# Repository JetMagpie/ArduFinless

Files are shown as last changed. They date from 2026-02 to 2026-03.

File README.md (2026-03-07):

# ArduFinless
An arduino based finless flying wing project, includes sideslip angle detection and drag rudder control law design.

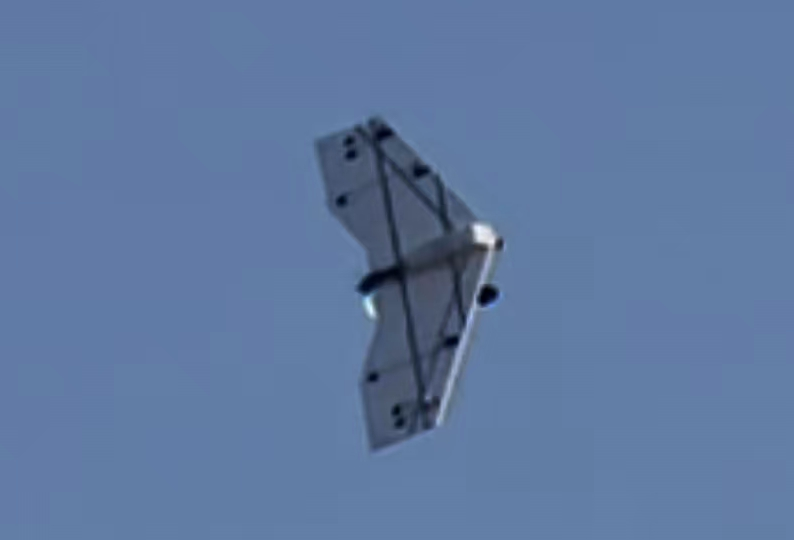
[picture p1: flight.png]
flight


**All engineering source files (.dxf, .step, .stp, .stl, .cpp, .h, .ino) of this project are licensed under the CERN-OHL-S-2.0 license, unless otherwise stated within the specific file.**

# Setup
The default code is written for arduino mega 2560 with a AS5047p as sideslip angle sensor and a mpu6500 as gyro. The sideslip angle sensor needs 4 m2.5x4 screws, a m3*10 screw and two 5x8x2 bearings to assemble. 

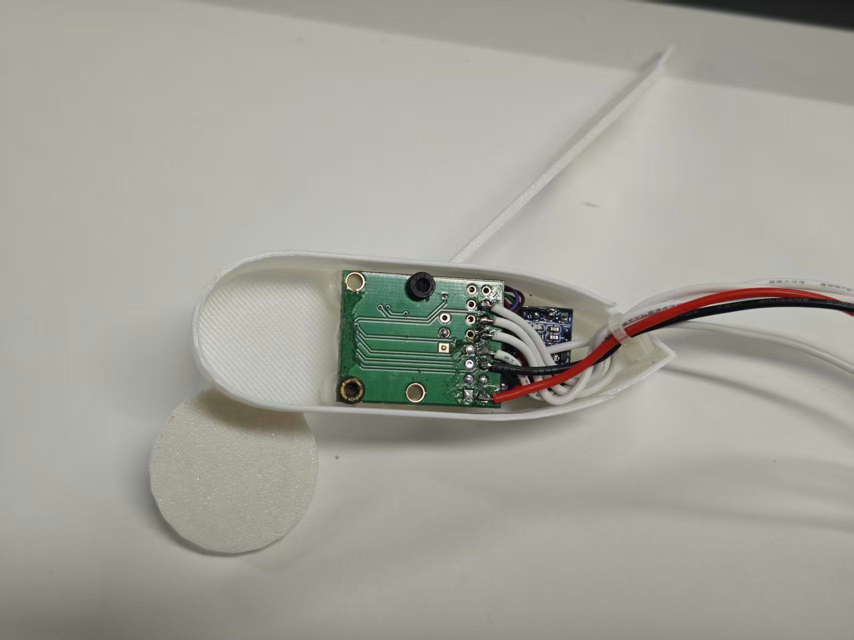
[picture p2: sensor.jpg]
sensor


The default airframe is made of 2mm foam board (vector board, depron, etc.) and 2mm carbon fiber rods. A detailed STP file and a laser engraver friendly dxf file are provided. Recommended electronic devices are KST ds113mg servos, xing2205 motor with 5040 propeller (20a ESC recommended) and 1000mAh3S LiPo battery. 

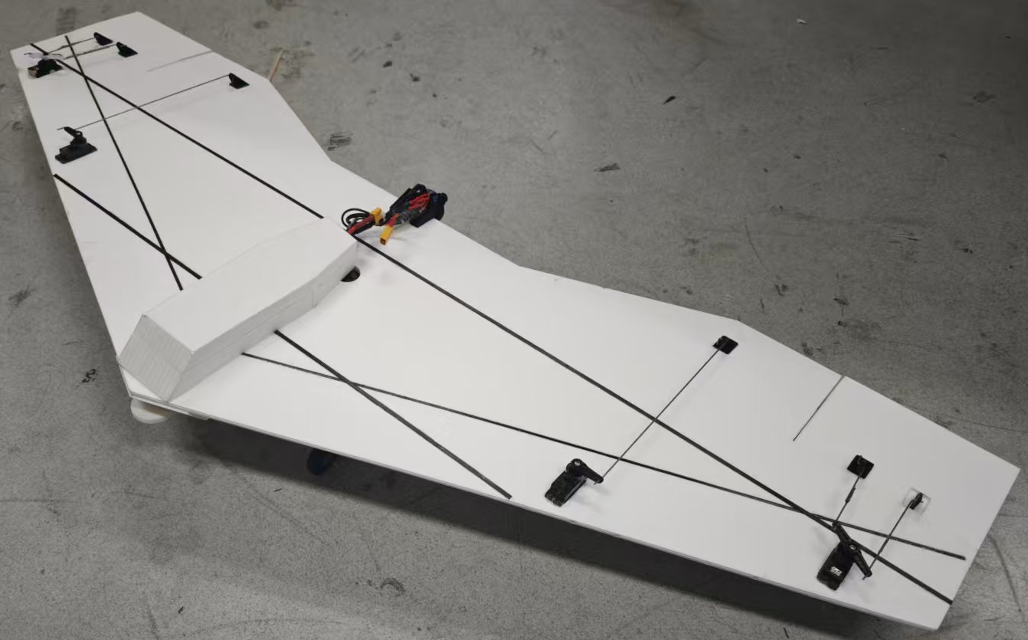
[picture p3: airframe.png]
airframe


The wiring is shown in this figure:

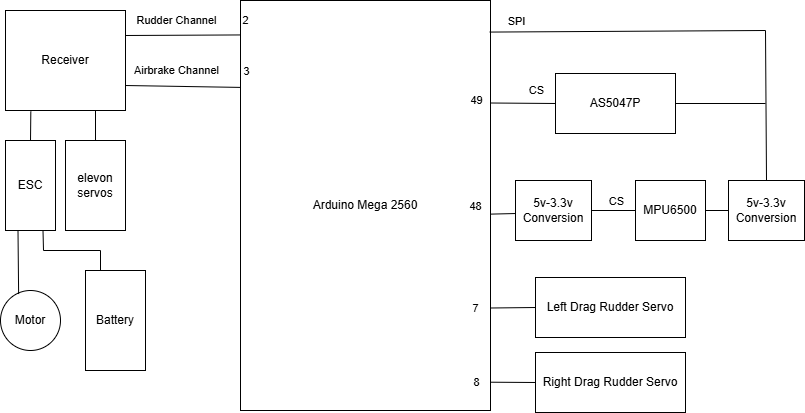
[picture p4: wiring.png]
wiring


# Parameters
Parameters can be changed via serial (baud rate 115200), send `help` to serial to see instructions.

It is recommended to change `right_lim_inf`, `right_lim_sup`, `left_lim_inf`, `left_lim_sup` to fit your servo installation, change `encoder_calibration` and `gyro_calibration` to fit your sensor installation, and change `Cn_beta` (coefficient of sideslip angle) and `Cn_damper` (coefficient of yaw rate) to fit your aircraft design. `Cn_y` can be used as an alternative of `Cn_beta`, it estimates beta with lateral acceleration.

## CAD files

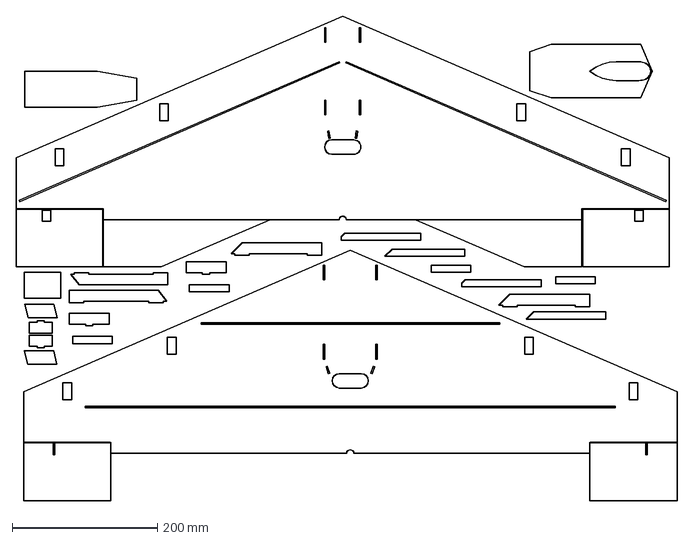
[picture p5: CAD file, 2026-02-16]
miniflywing_2mm.dxf
910.5 x 666.9 mm

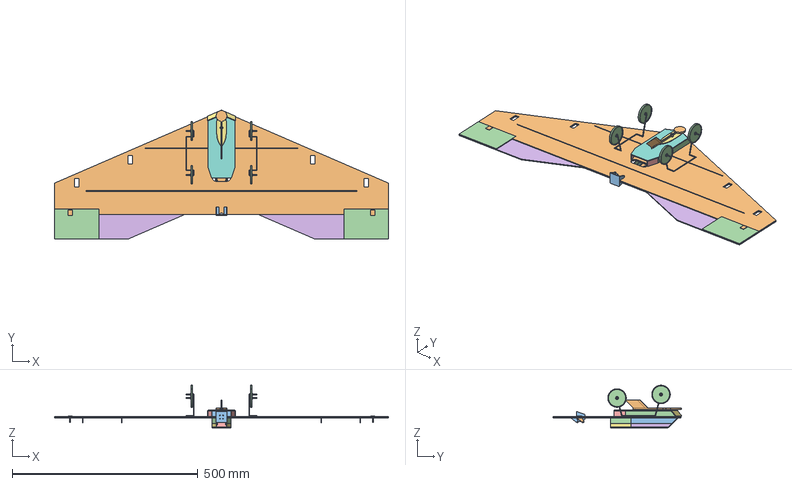
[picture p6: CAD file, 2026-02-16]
miniflywing.stp
900.0 x 346.5 x 115.0 mm

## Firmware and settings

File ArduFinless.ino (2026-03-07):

/*
 * 主程序：阻力舵飞翼控制程序（带串口调参与EEPROM存储）
 * 功能：
 * 1. 读取AS5047P磁编码器角度并处理过零点
 * 2. 读取MPU6500陀螺仪Z轴角速度
 * 3. 读取PWM输入并归一化
 * 4. 所有传感器输入经过低通滤波
 * 5. 根据阻力舵控制律计算右左输出值
 * 6. 输出PWM控制信号
 * 7. 串口调参：report/get/set/help/params
 * 8. 参数自动保存到EEPROM（启动时加载）
 */

#include <Arduino.h>
#include <SPI.h>
#include <EEPROM.h>
#include "PWM_IO.h"
#include "MPU6500.h"
#include "AS5047P.h" 
#include "LowPassFilter.h"

// ==================== 引脚定义 ====================
#define ENCODER_CS_PIN 49  // AS5047P的CS引脚
#define IMU_CS_PIN 48      // MPU6500的CS引脚

// ==================== 全局对象 ====================
PWM_IO pwmIO;
MPU6500 imu(IMU_CS_PIN, false); // 使用MPU6500库
AS5047P encoder(ENCODER_CS_PIN); // 使用AS5047P库

// ==================== 低通滤波器实例 ====================
const float SAMPLE_TIME = 0.01f;       // 采样时间10ms (100Hz)
float beta_cutoff_freq = 50.0f;        // 角度截止频率 (Hz)
float gyro_cutoff_freq = 50.0f;        // 角速度截止频率 (Hz)
float yaw_cutoff_freq = 80.0f;         // Yaw输入截止频率 (Hz)
float brake_cutoff_freq = 80.0f;       // Brake输入截止频率 (Hz)
float accel_cutoff_freq = 50.0f;       // 侧力截止频率 (Hz)

LowPassFilter beta_filter(beta_cutoff_freq, SAMPLE_TIME);
LowPassFilter gyro_filter(gyro_cutoff_freq, SAMPLE_TIME);
LowPassFilter accel_filter(accel_cutoff_freq, SAMPLE_TIME);

// ==================== 可调参数（将存入EEPROM）====================
// 这些全局变量将在加载EEPROM后被赋值
uint16_t right_lim_inf = 1600;   // 右输出最小脉冲宽度（微秒）
uint16_t right_lim_sup = 1800;   // 右输出最大脉冲宽度（微秒）
uint16_t left_lim_inf = 1200;    // 左输出最小脉冲宽度（微秒）
uint16_t left_lim_sup = 1400;    // 左输出最大脉冲宽度（微秒）
float encoder_calibration = 0.0f;// 编码器角度校准量（度）
float gyro_calibration = 0.0f;   // 陀螺仪角速度校准量（度/秒）
float Cn_beta = 5.0f;            // 角度反馈增益
float Cn_damper = 1.0f;          // 阻尼增益
float Cn_y = 1.0f;               // 侧力补偿

// 固定参数
float Yaw_gain = 1.0f;                 // 摇杆增益

// ==================== EEPROM 存储相关 ====================
#define EEPROM_MAGIC 0xDEADBEEF        // 用于校验EEPROM是否有效

// 参数结构体（紧凑排列，无填充）
struct SystemParams {
    uint16_t right_lim_inf;
    uint16_t right_lim_sup;
    uint16_t left_lim_inf;
    uint16_t left_lim_sup;
    float encoder_calibration;
    float gyro_calibration;
    float Cn_beta;
    float Cn_damper;
    float Cn_y;
} __attribute__((packed));

// 配置结构体（包含魔法数）
struct Config {
    uint32_t magic;
    SystemParams params;
} __attribute__((packed));

// 参数名称与范围（用于串口调参）
const char* param_names[] = {
    "right_lim_inf",
    "right_lim_sup", 
    "left_lim_inf",
    "left_lim_sup",
    "encoder_calibration",
    "gyro_calibration",
    "Cn_beta",
    "Cn_damper",
    "Cn_y"
};

struct ParamRange {
    float min;
    float max;
};

const ParamRange param_ranges[] = {
    {800, 2200},   // right_lim_inf
    {800, 2200},   // right_lim_sup
    {800, 2200},   // left_lim_inf
    {800, 2200},   // left_lim_sup
    {-360.0, 360.0},     // encoder_calibration
    {-10.0, 10.0},       // gyro_calibration
    {-50.0, 50.0},       // Cn_beta
    {-50.0, 50.0},       // Cn_damper
    {-50.0, 50.0}        // Cn_y
};
const int NUM_PARAMS = sizeof(param_names) / sizeof(char*);

// 默认参数值（与初始化值一致）
const SystemParams DEFAULT_PARAMS = {
    1600,   // right_lim_inf
    1800,   // right_lim_sup
    1200,    // left_lim_inf
    1400,   // left_lim_sup
    0.0f, // encoder_calibration
    0.0f,    // gyro_calibration
    5.0f,    // Cn_beta
    1.0f,    // Cn_damper
    1.0f     //Cn_y
};

// 串口命令相关
volatile bool report_enabled = false;   // 默认关闭调试打印
char serial_buffer[64];
uint8_t serial_index = 0;

// ==================== 函数声明 ====================
float readEncoderAngle(float calibration);
float readGyroRate(float calibration);
float readAccelY();
void readPWMInputs(float& Yaw, float& Brake);
void calculateOutputs(float Yaw, float Brake, float Beta, float Yaw_Rate, 
                     float Yaw_gain, float Cn_beta, float Cn_damper,
                     float& OUT_right, float& OUT_left);
void setPWMOutputs(float OUT_right, float OUT_left,
                   uint16_t right_lim_inf, uint16_t right_lim_sup,
                   uint16_t left_lim_inf, uint16_t left_lim_sup);
float normalizeAngle(float angle_deg);
void printDebugInfo(float Beta_raw, float Beta_filtered, float Yaw_Rate_raw, float Yaw_Rate_filtered,
                    float Yaw_raw, float Yaw_filtered, float Brake_raw, float Brake_filtered,
                    float OUT_right, float OUT_left);

// 新增串口与EEPROM函数
void loadParamsFromEEPROM();
void saveParamsToEEPROM();
void processSerialInput();
void processSerialCommand();
bool validateParam(int index, float value);
void printAllParams();

// ==================== 主程序 ====================

void setup() {
  // 初始化串口通信
  Serial.begin(115200);
  delay(100);
  
  // 从EEPROM加载参数（会更新全局变量）
  loadParamsFromEEPROM();
 
  // 初始化PWM输入输出
  pwmIO.begin();
  Serial.println("PWM IO initialized");
  
  // 初始化SPI
  SPI.begin();
  SPI.setClockDivider(SPI_CLOCK_DIV128);  // 设置100kHz时钟
  
  // 初始化磁编码器
  if (encoder.init()) {
    Serial.println("AS5047P initialized");
  } else {
    Serial.println("AS5047P initialization failed");
  }
  
  // 初始化陀螺仪
  if (imu.init()) {
    Serial.println("MPU6500 initialized");
  } else {
    Serial.println("MPU6500 initialization failed");
  }
  
  // 启用所有PWM输出通道
  pwmIO.enableOutput(1);
  pwmIO.enableOutput(2);
  pwmIO.enableOutput(3);
  pwmIO.enableOutput(4);
  
  Serial.println("System initialized");
  Serial.println("Serial commands: report on/off, get <param>, set <param> <value>, help, params");
  Serial.println("Data reporting is OFF by default. Use 'report on' to enable.");
  Serial.println("===================================");
  delay(1000);
}

void loop() {
  static uint32_t last_print_time = 0;
  static uint32_t last_update_time = 0;
  
  // 处理串口输入（调参命令）
  processSerialInput();
  
  // 检查PWM输入超时
  pwmIO.checkTimeouts();
  
  // 读取编码器原始角度（Beta）
  float Beta_raw = readEncoderAngle(encoder_calibration);
  
  // 读取陀螺仪原始角速度（Yaw_Rate）
  float Yaw_Rate_raw = readGyroRate(gyro_calibration);

    // 读取陀螺仪原始侧力(Accel_y)
  float Accel_y_raw = readAccelY();
  
  // 读取PWM输入（Yaw和Brake）
  float Yaw = 0.0f, Brake = 0.0f;
  readPWMInputs(Yaw, Brake);
  
  // 应用低通滤波
  float Beta = beta_filter.update(Beta_raw);
  float Yaw_Rate = gyro_filter.update(Yaw_Rate_raw);
  float Accel_y = accel_filter.update(Accel_y_raw);
  
  // 计算输出值
  static float OUT_right = 0.0f;
  static float OUT_left = 0.0f;
  calculateOutputs(Yaw, Brake, Beta, Yaw_Rate, Accel_y, 
                  Yaw_gain, Cn_beta, Cn_damper, Cn_y, 
                  OUT_right, OUT_left);
  
  // 设置PWM输出（使用当前全局限幅参数）
  setPWMOutputs(OUT_right, OUT_left,
                right_lim_inf, right_lim_sup,
                left_lim_inf, left_lim_sup);
 
  // 控制循环频率（100Hz）
  uint32_t current_time = millis();
  unsigned long delay_time = min(10, max(0, 10 - (current_time - last_update_time)));
  delay(delay_time);
  last_update_time = current_time;

  // 仅当报告启用时打印调试信息（每50ms）
  if (report_enabled && (current_time - last_print_time >= 50)) {
    printDebugInfo(Beta_raw, Beta, Yaw_Rate_raw, Yaw_Rate, Accel_y_raw, Accel_y, 
                   Yaw, Brake, OUT_right, OUT_left);
    last_print_time = current_time;
  }
}

// ==================== 原功能函数实现 ====================

float readEncoderAngle(float calibration) {
  if (encoder.read_angle()) {
    float angle_deg = encoder.get_angle_deg();
    angle_deg += calibration;
    angle_deg = normalizeAngle(angle_deg);
    return angle_deg;
  }
  Serial.println("AS5047P Error");
  return 0.0f;
}

float readGyroRate(float calibration) {
  if (imu.read_sensors()) {
    float gyro_z = imu.get_gyro_z();
    gyro_z += calibration;
    return gyro_z;
  }
  Serial.println("MPU6500 Error");
  return 0.0f;
}

float readAccelY() {
  if (imu.read_sensors()) {
    float accel_y = imu.get_accel_x();
    return accel_y;
  }
  Serial.println("MPU6500 Error");
  return 0.0f;
}

void readPWMInputs(float& Yaw, float& Brake) {
  if (pwmIO.isCH1_Valid()) {
    uint16_t pulse_width1 = pwmIO.getCH1_IN();
    Yaw = (pulse_width1 - 1500.0f) / 350.0f;
    Yaw = constrain(Yaw, -1.0f, 1.0f);
  } else {
    Yaw = 0.0f;
  }
  
  if (pwmIO.isCH2_Valid()) {
    uint16_t pulse_width2 = pwmIO.getCH2_IN();
    Brake = (pulse_width2 - 1500.0f) / 350.0f;
    Brake = constrain(Brake, -1.0f, 1.0f);
  } else {
    Brake = 0.0f;
  }
}

void calculateOutputs(float Yaw, float Brake, float Beta, float Yaw_Rate, float Accel_y, 
                     float Yaw_gain, float Cn_beta, float Cn_damper, float Cn_y, 
                     float& OUT_right, float& OUT_left) {
  float Beta_norm = Beta / 180.0f;
  Beta_norm = constrain(Beta_norm, -1.0f, 1.0f);
  
  float Yaw_Rate_norm = Yaw_Rate / 180.0f;
  Yaw_Rate_norm = constrain(Yaw_Rate_norm, -1.0f, 1.0f);

  float Accel_y_norm = Accel_y / 2.0f;
  Accel_y_norm = constrain(Accel_y_norm, -1.0f, 1.0f);
  
  float control_term = - Yaw * Yaw_gain - Beta_norm * Cn_beta + Yaw_Rate_norm * Cn_damper + Accel_y_norm * Cn_y;
  float control_clamped = constrain(control_term, -1.0f, 1.0f);
  
  float brake_clamped = constrain(Brake, 0.0f, 1.0f);

  OUT_right = constrain(control_clamped + brake_clamped, 0.0f, 1.0f);
  OUT_left = constrain(-control_clamped + brake_clamped, 0.0f, 1.0f);
}

void setPWMOutputs(float OUT_right, float OUT_left,
                   uint16_t right_lim_inf, uint16_t right_lim_sup,
                   uint16_t left_lim_inf, uint16_t left_lim_sup) {
  OUT_right = constrain(OUT_right, 0.0f, 1.0f);
  OUT_left = constrain(OUT_left, 0.0f, 1.0f);
  
  uint16_t right_pulse = map(OUT_right * 1000, 1000, 0, right_lim_inf, right_lim_sup);
  uint16_t left_pulse = map(OUT_left * 1000, 0, 1000, left_lim_inf, left_lim_sup);
  
  pwmIO.setCH3_OUT(right_pulse);
  pwmIO.setCH4_OUT(left_pulse);
}

float normalizeAngle(float angle_deg) {
  angle_deg = fmod(angle_deg, 360.0f);
  if (angle_deg < 0) angle_deg += 360.0f;
  if (angle_deg > 180.0f) angle_deg -= 360.0f;
  return angle_deg;
}

void printDebugInfo(float Beta_raw, float Beta_filtered, float Yaw_Rate_raw, float Yaw_Rate_filtered, float Accel_y_raw, float Accel_y_filtered, 
                    float Yaw, float Brake,
                    float OUT_right, float OUT_left) {
  Serial.print("Beta: ");
  Serial.print(Beta_raw, 1);
  Serial.print("(");
  Serial.print(Beta_filtered, 1);
  Serial.print(") | Yaw_Rate: ");
  Serial.print(Yaw_Rate_raw, 2);
  Serial.print("(");
  Serial.print(Yaw_Rate_filtered, 2);
  Serial.print(") | Yaw: ");
  Serial.print(") | Accel_y: ");
  Serial.print(Accel_y_raw, 2);
  Serial.print("(");
  Serial.print(Accel_y_filtered, 2);
  Serial.print(") | Yaw: ");
  Serial.print(Yaw, 3);
  Serial.print(" | Brake: ");
  Serial.print(Brake, 3);
  Serial.print("R_OUT: ");
  Serial.print(OUT_right, 3);
  Serial.print(" | L_OUT: ");
  Serial.print(OUT_left, 3);
  Serial.println();
}

// ==================== 串口与EEPROM函数 ====================

void loadParamsFromEEPROM() {
  Config config;
  EEPROM.get(0, config);
  
  if (config.magic == EEPROM_MAGIC) {
    bool valid = true;
    
    // 逐个验证参数
    if (config.params.right_lim_inf < param_ranges[0].min || config.params.right_lim_inf > param_ranges[0].max) valid = false;
    if (config.params.right_lim_sup < param_ranges[1].min || config.params.right_lim_sup > param_ranges[1].max) valid = false;
    if (config.params.left_lim_inf < param_ranges[2].min || config.params.left_lim_inf > param_ranges[2].max) valid = false;
    if (config.params.left_lim_sup < param_ranges[3].min || config.params.left_lim_sup > param_ranges[3].max) valid = false;
    if (config.params.encoder_calibration < param_ranges[4].min || config.params.encoder_calibration > param_ranges[4].max) valid = false;
    if (config.params.gyro_calibration < param_ranges[5].min || config.params.gyro_calibration > param_ranges[5].max) valid = false;
    if (config.params.Cn_beta < param_ranges[6].min || config.params.Cn_beta > param_ranges[6].max) valid = false;
    if (config.params.Cn_damper < param_ranges[7].min || config.params.Cn_damper > param_ranges[7].max) valid = false;
    if (config.params.Cn_y < param_ranges[8].min || config.params.Cn_y > param_ranges[8].max) valid = false;
    
    if (valid) {
      right_lim_inf = config.params.right_lim_inf;
      right_lim_sup = config.params.right_lim_sup;
      left_lim_inf = config.params.left_lim_inf;
      left_lim_sup = config.params.left_lim_sup;
      encoder_calibration = config.params.encoder_calibration;
      gyro_calibration = config.params.gyro_calibration;
      Cn_beta = config.params.Cn_beta;
      Cn_damper = config.params.Cn_damper;
      Cn_y = config.params.Cn_y;
      
      Serial.println("Parameters loaded from EEPROM");
      return;
    } else {
      Serial.println("EEPROM data out of range, using defaults");
    }
  } else {
    Serial.println("EEPROM magic mismatch, using defaults");
  }
  
  // 使用默认参数并保存
  right_lim_inf = DEFAULT_PARAMS.right_lim_inf;
  right_lim_sup = DEFAULT_PARAMS.right_lim_sup;
  left_lim_inf = DEFAULT_PARAMS.left_lim_inf;
  left_lim_sup = DEFAULT_PARAMS.left_lim_sup;
  encoder_calibration = DEFAULT_PARAMS.encoder_calibration;
  gyro_calibration = DEFAULT_PARAMS.gyro_calibration;
  Cn_beta = DEFAULT_PARAMS.Cn_beta;
  Cn_damper = DEFAULT_PARAMS.Cn_damper;
  Cn_y = DEFAULT_PARAMS.Cn_y;
  
  saveParamsToEEPROM();
}


void saveParamsToEEPROM() {
  Config config;
  config.magic = EEPROM_MAGIC;
  config.params.right_lim_inf = right_lim_inf;
  config.params.right_lim_sup = right_lim_sup;
  config.params.left_lim_inf = left_lim_inf;
  config.params.left_lim_sup = left_lim_sup;
  config.params.encoder_calibration = encoder_calibration;
  config.params.gyro_calibration = gyro_calibration;
  config.params.Cn_beta = Cn_beta;
  config.params.Cn_damper = Cn_damper;
  config.params.Cn_y = Cn_y;
  
  EEPROM.put(0, config);
  Serial.println("Parameters saved to EEPROM");
}

bool validateParam(int index, float value) {
  if (index < 0 || index >= NUM_PARAMS) return false;
  return (value >= param_ranges[index].min && value <= param_ranges[index].max);
}

void processSerialInput() {
  while (Serial.available() > 0) {
    char c = Serial.read();
    if (c == '\r' || c == '\n') {
      if (serial_index > 0) {
        serial_buffer[serial_index] = '\0';
        processSerialCommand();
        serial_index = 0;
      }
    } else if (serial_index < sizeof(serial_buffer) - 1) {
      serial_buffer[serial_index++] = c;
    }
  }
}

void processSerialCommand() {
  char* token = strtok(serial_buffer, " ");
  if (token == NULL) return;
  
  if (strcmp(token, "report") == 0) {
    token = strtok(NULL, " ");
    if (token != NULL) {
      if (strcmp(token, "on") == 0) {
        report_enabled = true;
        Serial.println("Report enabled");
      } else if (strcmp(token, "off") == 0) {
        report_enabled = false;
        Serial.println("Report disabled");
      }
    }
  }
  else if (strcmp(token, "get") == 0) {
    token = strtok(NULL, " ");
    if (token != NULL) {
      for (int i = 0; i < NUM_PARAMS; i++) {
        if (strcmp(token, param_names[i]) == 0) {
          float val;
          switch (i) {
            case 0: val = right_lim_inf; break;
            case 1: val = right_lim_sup; break;
            case 2: val = left_lim_inf; break;
            case 3: val = left_lim_sup; break;
            case 4: val = encoder_calibration; break;
            case 5: val = gyro_calibration; break;
            case 6: val = Cn_beta; break;
            case 7: val = Cn_damper; break;
            case 8: val = Cn_y; break;
            default: val = 0;
          }
          Serial.print(param_names[i]);
          Serial.print(" = ");
          Serial.println(val, 4);
          return;
        }
      }
      Serial.print("Unknown parameter: ");
      Serial.println(token);
    }
  }
  else if (strcmp(token, "set") == 0) {
    token = strtok(NULL, " ");
    if (token != NULL) {
      char* param_name = token;
      token = strtok(NULL, " ");
      if (token != NULL) {
        float new_value = atof(token);
        
        for (int i = 0; i < NUM_PARAMS; i++) {
          if (strcmp(param_name, param_names[i]) == 0) {
            if (!validateParam(i, new_value)) {
              Serial.print("Value out of range! Valid range: ");
              Serial.print(param_ranges[i].min);
              Serial.print(" to ");
              Serial.println(param_ranges[i].max);
              return;
            }
            
            // 更新对应全局变量
            switch (i) {
              case 0: right_lim_inf = (uint16_t)round(new_value); break;
              case 1: right_lim_sup = (uint16_t)round(new_value); break;
              case 2: left_lim_inf = (uint16_t)round(new_value); break;
              case 3: left_lim_sup = (uint16_t)round(new_value); break;
              case 4: encoder_calibration = new_value; break;
              case 5: gyro_calibration = new_value; break;
              case 6: Cn_beta = new_value; break;
              case 7: Cn_damper = new_value; break;
              case 8: Cn_y = new_value; break;
            }
            
            // 保存到EEPROM
            saveParamsToEEPROM();
            
            Serial.print("Set ");
            Serial.print(param_names[i]);
            Serial.print(" to ");
            Serial.println(new_value, 4);
            return;
          }
        }
        Serial.print("Unknown parameter: ");
        Serial.println(param_name);
      }
    }
  }
  else if (strcmp(token, "help") == 0) {
    Serial.println("Available commands:");
    Serial.println("  report on/off - Enable/disable data reporting");
    Serial.println("  get <param>   - Get parameter value");
    Serial.println("  set <param> <value> - Set parameter value");
    Serial.println("  params        - List all parameters with ranges");
    Serial.println("  help          - Show this help");
  }
  else if (strcmp(token, "params") == 0) {
    printAllParams();
  }
  else {
    Serial.print("Unknown command: ");
    Serial.println(token);
    Serial.println("Type 'help' for available commands");
  }
}

void printAllParams() {
  Serial.println("Available parameters (current value | range):");
  for (int i = 0; i < NUM_PARAMS; i++) {
    float val;
    switch (i) {
      case 0: val = right_lim_inf; break;
      case 1: val = right_lim_sup; break;
      case 2: val = left_lim_inf; break;
      case 3: val = left_lim_sup; break;
      case 4: val = encoder_calibration; break;
      case 5: val = gyro_calibration; break;
      case 6: val = Cn_beta; break;
      case 7: val = Cn_damper; break;
      case 8: val = Cn_y; break;
      default: val = 0;
    }
    Serial.print("  ");
    Serial.print(param_names[i]);
    Serial.print(" = ");
    Serial.print(val, 4);
    Serial.print("  [");
    Serial.print(param_ranges[i].min);
    Serial.print(", ");
    Serial.print(param_ranges[i].max);
    Serial.println("]");
  }
}

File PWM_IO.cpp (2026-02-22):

#include "PWM_IO.h"
#include <avr/interrupt.h>
#include <util/atomic.h>

// 初始化静态实例指针
PWM_IO* PWM_IO::instance = nullptr;

// 构造函数
PWM_IO::PWM_IO() {
    // 初始化输入相关变量
    ch1_rise_time = 0;
    ch1_pulse_width = DEFAULT_PWM_WIDTH;
    ch1_valid = false;
    ch1_last_update = 0;
    
    ch2_rise_time = 0;
    ch2_pulse_width = DEFAULT_PWM_WIDTH;
    ch2_valid = false;
    ch2_last_update = 0;
    
    ch3_rise_time = 0;
    ch3_pulse_width = DEFAULT_PWM_WIDTH;
    ch3_valid = false;
    ch3_last_update = 0;
    
    ch4_rise_time = 0;
    ch4_pulse_width = DEFAULT_PWM_WIDTH;
    ch4_valid = false;
    ch4_last_update = 0;
    
    // 初始化输出相关变量为默认值
    ch1_out_width = DEFAULT_PWM_WIDTH;
    ch2_out_width = DEFAULT_PWM_WIDTH;
    ch3_out_width = DEFAULT_PWM_WIDTH;
    ch4_out_width = DEFAULT_PWM_WIDTH;
    
    // 设置实例指针
    instance = this;
}

// 初始化函数
void PWM_IO::begin() {
    // 配置输入引脚为输入模式，启用上拉电阻
    pinMode(CH1_IN_PIN, INPUT);
    pinMode(CH2_IN_PIN, INPUT);
    pinMode(CH3_IN_PIN, INPUT);
    pinMode(CH4_IN_PIN, INPUT);
    
    // 配置输出引脚
    pinMode(CH1_OUT_PIN, OUTPUT);
    pinMode(CH2_OUT_PIN, OUTPUT);
    pinMode(CH3_OUT_PIN, OUTPUT);
    pinMode(CH4_OUT_PIN, OUTPUT);
    
    // 配置定时器
    configureTimer1();
    configureTimer4();
    
    // 配置中断（使用CHANGE模式）
    // CH1 (Pin 2) - 外部中断0
    attachInterrupt(digitalPinToInterrupt(CH1_IN_PIN), isrCH1_Change, CHANGE);
    
    // CH2 (Pin 3) - 外部中断1
    attachInterrupt(digitalPinToInterrupt(CH2_IN_PIN), isrCH2_Change, CHANGE);
    
    // CH3 (Pin 18) - 外部中断5
    attachInterrupt(digitalPinToInterrupt(CH3_IN_PIN), isrCH3_Change, CHANGE);
    
    // CH4 (Pin 19) - 外部中断4
    attachInterrupt(digitalPinToInterrupt(CH4_IN_PIN), isrCH4_Change, CHANGE);
    
    // 记录初始时间
    uint32_t now = millis();
    ch1_last_update = now;
    ch2_last_update = now;
    ch3_last_update = now;
    ch4_last_update = now;
    
    // 确保中断使能
    sei();
}

// 配置Timer1用于输出50Hz PWM（引脚11、12）
void PWM_IO::configureTimer1() {
    cli();
    
    TCCR1A = 0;
    TCCR1B = 0;
    TCNT1 = 0;
    
    // 模式14：快速PWM，TOP=ICR1
    // COM1A1:1 COM1B1:1 - 非反相模式，引脚11和12输出PWM
    TCCR1A = (1 << COM1A1) | (1 << COM1B1) | (1 << WGM11);
    TCCR1B = (1 << WGM13) | (1 << WGM12) | (1 << CS11);  // 预分频8
    
    // 舵机需要10ms周期，使用0.5us分辨率：10000us / 0.5us = 20000
    ICR1 = 20000;  // TOP值，对应10ms周期
    
    // 初始占空比设置为0（舵机不输出）
    OCR1A = 0xFFFF;  // 引脚12
    OCR1B = 0xFFFF;  // 引脚11
    
    sei();
}

// 配置Timer4用于输出50Hz PWM（引脚7、8）
void PWM_IO::configureTimer4() {
    cli();
    
    TCCR4A = 0;
    TCCR4B = 0;
    TCNT4 = 0;
    
    // 模式14：快速PWM，TOP=ICR4
    TCCR4A = (1 << COM4A1) | (1 << COM4B1) | (1 << COM4C1) | (1 << WGM41);
    TCCR4B = (1 << WGM43) | (1 << WGM42) | (1 << CS41);  // 预分频8
    
    ICR4 = 20000;  // TOP值，对应10ms周期
    
    // 初始占空比设置为0（舵机不输出）
    OCR4A = 0xFFFF;  // 引脚6（CH5，未使用）
    OCR4B = 0xFFFF;  // 引脚7（CH4）
    OCR4C = 0xFFFF;  // 引脚8（CH3）
    
    sei();
}

// 约束脉冲宽度到800-2200μs范围
uint16_t PWM_IO::constrainPulse(uint16_t pulse_us) {
    if (pulse_us < MIN_PWM_WIDTH) return MIN_PWM_WIDTH;
    if (pulse_us > MAX_PWM_WIDTH) return MAX_PWM_WIDTH;
    return pulse_us;
}

// 将脉冲宽度（μs）转换为OCR值（0.5μs单位）
uint16_t PWM_IO::pulseToOCR(uint16_t pulse_us) {
    // 约束范围
    pulse_us = constrainPulse(pulse_us);
    
    // 转换为0.5us单位：pulse_us * 2
    return pulse_us << 1;
}

// 设置输出PWM宽度
void PWM_IO::setCH1_OUT(uint16_t highTime_us) {
    ch1_out_width = constrainPulse(highTime_us);
    uint16_t ocr_value = pulseToOCR(ch1_out_width);
    
    cli();
    OCR1B = ocr_value;  // 引脚11，定时器1B
    sei();
}

void PWM_IO::setCH2_OUT(uint16_t highTime_us) {
    ch2_out_width = constrainPulse(highTime_us);
    uint16_t ocr_value = pulseToOCR(ch2_out_width);
    
    cli();
    OCR1A = ocr_value;  // 引脚12，定时器1A
    sei();
}

void PWM_IO::setCH3_OUT(uint16_t highTime_us) {
    ch3_out_width = constrainPulse(highTime_us);
    uint16_t ocr_value = pulseToOCR(ch3_out_width);
    
    cli();
    OCR4C = ocr_value;  // 引脚8，定时器4C
    sei();
}

void PWM_IO::setCH4_OUT(uint16_t highTime_us) {
    ch4_out_width = constrainPulse(highTime_us);
    uint16_t ocr_value = pulseToOCR(ch4_out_width);
    
    cli();
    OCR4B = ocr_value;  // 引脚7，定时器4B
    sei();
}

// 启用输出通道
void PWM_IO::enableOutput(uint8_t channel) {
    switch(channel) {
        case 1:  // CH1 (引脚11)
            TCCR1A |= (1 << COM1B1);
            break;
        case 2:  // CH2 (引脚12)
            TCCR1A |= (1 << COM1A1);
            break;
        case 3:  // CH3 (引脚8)
            TCCR4A |= (1 << COM4C1);
            break;
        case 4:  // CH4 (引脚7)
            TCCR4A |= (1 << COM4B1);
            break;
    }
}

// 禁用输出通道
void PWM_IO::disableOutput(uint8_t channel) {
    switch(channel) {
        case 1:  // CH1 (引脚11)
            TCCR1A &= ~(1 << COM1B1);
            digitalWrite(CH1_OUT_PIN, LOW);
            break;
        case 2:  // CH2 (引脚12)
            TCCR1A &= ~(1 << COM1A1);
            digitalWrite(CH2_OUT_PIN, LOW);
            break;
        case 3:  // CH3 (引脚8)
            TCCR4A &= ~(1 << COM4C1);
            digitalWrite(CH3_OUT_PIN, LOW);
            break;
        case 4:  // CH4 (引脚7)
            TCCR4A &= ~(1 << COM4B1);
            digitalWrite(CH4_OUT_PIN, LOW);
            break;
    }
}

// 中断服务函数实现（CHANGE模式）
void PWM_IO::isrCH1_Change() {
    if (instance) {
        if (digitalRead(CH1_IN_PIN)) {
            instance->ch1_rise_time = micros();
        } else {
            uint32_t pulse_width = micros() - instance->ch1_rise_time;
            if (pulse_width >= MIN_PWM_WIDTH && pulse_width <= MAX_PWM_WIDTH) {
                instance->ch1_pulse_width = pulse_width;
                instance->ch1_last_update = millis();
                instance->ch1_valid = true;
            }
        }
    }
}

void PWM_IO::isrCH2_Change() {
    if (instance) {
        if (digitalRead(CH2_IN_PIN)) {
            instance->ch2_rise_time = micros();
        } else {
            uint32_t pulse_width = micros() - instance->ch2_rise_time;
            if (pulse_width >= MIN_PWM_WIDTH && pulse_width <= MAX_PWM_WIDTH) {
                instance->ch2_pulse_width = pulse_width;
                instance->ch2_last_update = millis();
                instance->ch2_valid = true;
            }
        }
    }
}

void PWM_IO::isrCH3_Change() {
    if (instance) {
        if (digitalRead(CH3_IN_PIN)) {
            instance->ch3_rise_time = micros();
        } else {
            uint32_t pulse_width = micros() - instance->ch3_rise_time;
            if (pulse_width >= MIN_PWM_WIDTH && pulse_width <= MAX_PWM_WIDTH) {
                instance->ch3_pulse_width = pulse_width;
                instance->ch3_last_update = millis();
                instance->ch3_valid = true;
            }
        }
    }
}
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

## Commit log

2026-02-22 Add atomic protection to prevent servo shaking caused by pwm input and unstable power..
    [PWM_IO.cpp]
2026-02-23 Servo shaking bug fixed
    [ArduFinless.ino, PWM_IO.cpp]
2026-03-07 Added lateral acceleration control, removed filters for pwm input.
